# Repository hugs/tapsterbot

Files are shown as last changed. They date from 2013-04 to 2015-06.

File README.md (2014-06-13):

## Tapster - Mobile Automation Robot

<span>
    Tapsterbot
</span>

##Dependencies
- Node.js
- One Tapster robot

##Getting Started

1. Download and install the Arduino Client: [http://arduino.cc/en/Guide/HomePage](http://arduino.cc/en/Guide/HomePage)
2. Follow the setup procedure, and use the "blink" test script to verify your Arduino is working.
3. From the Arduino IDE upload the "Firmata" script: File -> Open -> Examples > Firmata > StandardFirmata
4. Install the dependencies: `cd software; npm install`
5. Start'er up: `node src/bot.js`
6. Start dancing: `dance()`
7. Stop dancing: `chill()`
8. Start moving: `go(0,0,-140)`

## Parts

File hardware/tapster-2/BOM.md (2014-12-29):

## Tapster Bill of Materials:

### Bitbeam
    3D Print:
    Qty     Description
    4       3x1 beam
    5       9x1 beam
    2       11x1 plate
    12      Coupler
    3       Servo mount
    1       Stylus holder
    3       Upper arm

    3D Print or Mill:
    Qty     Description
    1       Top plate
    1       Base plate
    3       Side plate
    1       Arduino plate

### Indigo.com
    Qty     Description                                             Part #          Unit Price
    24      Rod magnet, D5 x 7.5mm, Nd rare earth, N42              44201-7.5       $0.44

### McMaster-Carr
    Socket Bolts:
    Qty     Description     Long Description:                               Part #     Unit Price
    5       4-40 1/2 in     Black-Oxide Alloy Steel Socket Head Cap Screw   91251A110   $8.34 per pack of 100
    6       6-32 3/4 in     Black-Oxide Alloy Steel Socket Head Cap Screw   91251A151   $8.50 per pack of 100
    30      10-32 3/4 in    Black-Oxide Alloy Steel Socket Head Cap Screw   91251A345   $9.93 per pack of 100
    4       10-32 1 in      Black-Oxide Alloy Steel Socket Head Cap Screw   91251A347   $7.82 per pack of 50     

    Hex Nuts:
    Qty     Description             Long Description:                                       Part #      Unit Price
    5       4-40 nuts               Black Nylon 6/6 Hex Nut                                 94812A200   $5.63 per pack of 100
    6       6-32 nuts               Zinc-Plated Steel Machine Screw Hex Nut                 90480A007   $1.16 per pack of 100
    30      10-32 low-profile nuts  18-8 Stainless Steel Undersized Machine Screw Hex Nut   90730A411   $6.18 per pack of 100

    Misc:
    Qty     Description                                 Long Description:                   Part #      Unit Price
    12      3/8" Steel ball bearing                                                         96455K54    $5.87 per pack of 250
    6       12cm 6-32 Zinc-plated steel threaded rod    (Sold in 6ft sections)              98914A007   $3.67 for 6ft

### Servocity
    Qty     Description                                             Part #          Unit Price
    3       Hitec HS-311 servo (clockwise rotation)                 31311S00        $7.99

### Staples
    Qty     Description     Long Description                        Part #          Unit Price
    1       Tablet stylus   QVS ISE-SV Extending Mini-Stylus        IM1NZ0711       $3.99

## Electronics:

### Adafruit.com
    Qty     Description     Long Description                                    Part #          Unit Price
    1       Power adaptor   9 VDC 1000mA regulated switching power adapter      63              $6.95
    
### Amazon.com
    Qty     Description                                                         Part #          Unit Price
    1       SainSmart Sensor Shield Digital Analog Module V4                    B006TQ314G      $12.80

### Jameco.com
    Qty     Description             Long Description                            Part #          Unit Price
    1       Arduino Uno             MCU,ARDUINO UNO R3,DIP,14DI                 2151486         $29.95
    1       USB cable               CABLE,USB2.0,A/B,3',BLACK                   222608          $1.95
    1       Alligator clip          ALLIGATOR CLIP TEST LEADS, 24 AWG WIRE      2185483         $1.95

## Tools:

### McMaster-Carr
    Screwdrivers:
    Qty     Description         Long Description:                           Part #:     Unit Price:     Note:
    1       3/32 hex driver     Comfort Grip Ball Driver                    5497A25     $2.27           For 4-40 screws
    1       7/64 hex driver     Comfort Grip Ball Driver                    5497A26     $2.31           For 6-32 screws
    1       5/32 hex driver     Comfort Grip Ball Driver                    5497A29     $2.69           For 10-32 screws
    1       5/16 wrench         Miniature Inch Combination Wrench           5443A28     $10.69          For 10-32 nuts
    1       Philips #1 driver   Ultra-Grip Screwdriver with Antislip Tip    55095A32    $3.61           For servo mount

## Materials:
For 3D Printers:
ABS plastic from Ultimachine

For CNC Mills:
Plywood and Basswood from Blick Arts / Midwest Products

## Miscellaneous:

### Uline
    Qty     Description
    1       8X8x14 box
    1       Red bag

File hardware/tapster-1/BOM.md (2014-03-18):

## Tapster Bill of Materials:

### Bitbeam
    3D Print:
    Qty     Description
    12      2x1 beam
    8       3x1 beam
    6       5x1 beam
    5       9x1 beam
    2       11x1 plate
    6       17x1 plate
    3       Upper arm    
    3       Servo mount
    1       Stylus holder

    3D Print or Mill:
    Qty     Description
    3       5x29 side plate
    1       Arduino plate
    1       Base plate    
    1       Top plate

### McMaster-Carr
    Socket Bolts:
    Qty     Description     Long Description:                               Part #     Unit Price
    4       4-40 1/2 in     Black-Oxide Alloy Steel Socket Head Cap Screw   91251A110   $8.34 per pack of 100
    6       6-32 3/4 in     Black-Oxide Alloy Steel Socket Head Cap Screw   91251A151   $8.50 per pack of 100
    50      10-32 3/4 in    Black-Oxide Alloy Steel Socket Head Cap Screw   91251A345   $9.93 per pack of 100
    10      10-32 1 in      Black-Oxide Alloy Steel Socket Head Cap Screw   91251A347   $7.82 per pack of 50
    6       10-32 1 1/4 in  Black-Oxide Alloy Steel Socket Head Cap Screw   91251A349   $10.94 per pack of 50

    Hex Nuts:
    Qty     Description             Long Description:                                       Part #      Unit Price
    4       4-40 nuts               Black Nylon 6/6 Hex Nut                                 94900A005   $5.47 per pack of 100
    6       6-32 nuts               Zinc-Plated Steel Machine Screw Hex Nut                 90480A007   $1.16 per pack of 100
    48      10-32 low-profile nuts  18-8 Stainless Steel Undersized Machine Screw Hex Nut   90730A411   $6.18 per pack of 100
    18      10-32 lock nuts         Zinc-Plated Grade 2 Steel Nylon-Insert Hex Locknut      90631A411   $2.81 per pack of 100

### Jameco
    Qty     Description             Long Description                            Part #          Unit Price
    1       Arduino Uno             MCU,ARDUINO UNO R3,DIP,14DI                 2151486         $29.95
    1       Arduino proto-shield    SHIELD,PROTO,REV3,ASSEMBLED                 2152391         $15.95
    1       Breadboard              BREADBOARD,35x45x10mm,2.54mm HOLE SPACING   2109801         $4.95
    2       Jumper Wires            WIRE JUMPER REINFORCD,4"L,W/R               126342          $5.95
    1       USB cable               CABLE,USB2.0,A/B,3',BLACK                   222608          $1.95
    1       Alligator clip          ALLIGATOR CLIP TEST LEADS, 24 AWG WIRE      2185483         $1.95
    3       3-pin headers           HEADER,.1"ST MALE,1RW,3PIN                  109576          $0.35

### Servocity
    Qty     Description                                             Part #          Unit Price
    3       Hitec HS-311 servo (clockwise rotation)                 31311S00        $7.99

### Staples
    Qty     Description     Long Description                        Part #          Unit Price
    1       Tablet stylus   QVS ISE-SV Extending Mini-Stylus        IM1NZ0711       $3.99

## Tools:

### McMaster-Carr
    Screwdrivers:
    Qty     Description         Long Description:                           Part #:     Unit Price:     Note:
    1       3/32 hex driver     Comfort Grip Ball Driver                    5497A25     $2.27           For 4-40 screws
    1       7/64 hex driver     Comfort Grip Ball Driver                    5497A26     $2.31           For 6-32 screws
    1       5/32 hex driver     Comfort Grip Ball Driver                    5497A29     $2.69           For 10-32 screws
    1       3/8 nut driver      Comfort-Grip Inch NutdriversFor             53765A16    $3.58           For 10-32 lock nuts
    1       5/16 wrench         Miniature Inch Combination Wrench           5443A28     $10.69          For 10-32 nuts
    1       Philips #1 driver   Ultra-Grip Screwdriver with Antislip Tip    55095A32    $3.61           For servo mount

## Materials:
For 3D Printers:
ABS plastic from Ultimachine

For CNC Mills:
Plywood and Basswood from Blick Arts / Midwest Products

## Miscellaneous:

### Uline
    Qty     Description
    1       8X8x14 box
    1       Red bag

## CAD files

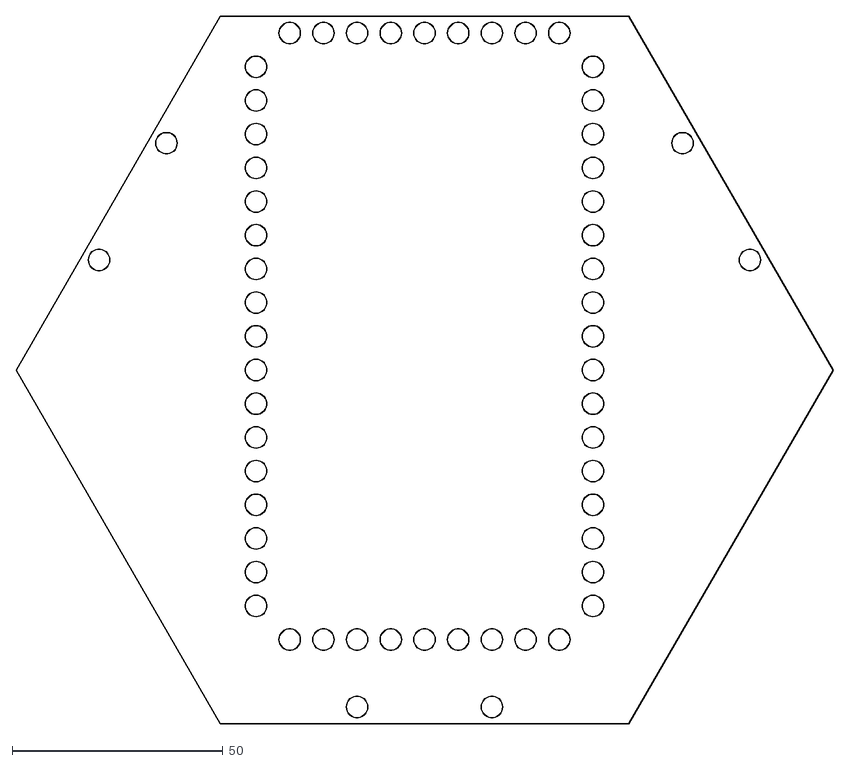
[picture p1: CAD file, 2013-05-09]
hardware/tapster-1/dxf/base.dxf
194.0 x 168.0

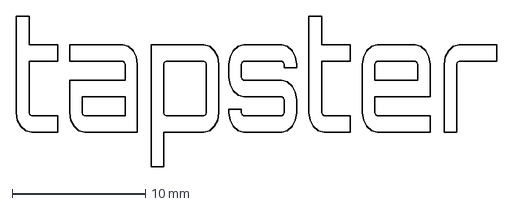
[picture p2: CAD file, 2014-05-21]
hardware/tapster-1/scad/tapster-smaller.dxf
36.1 x 11.3 mm

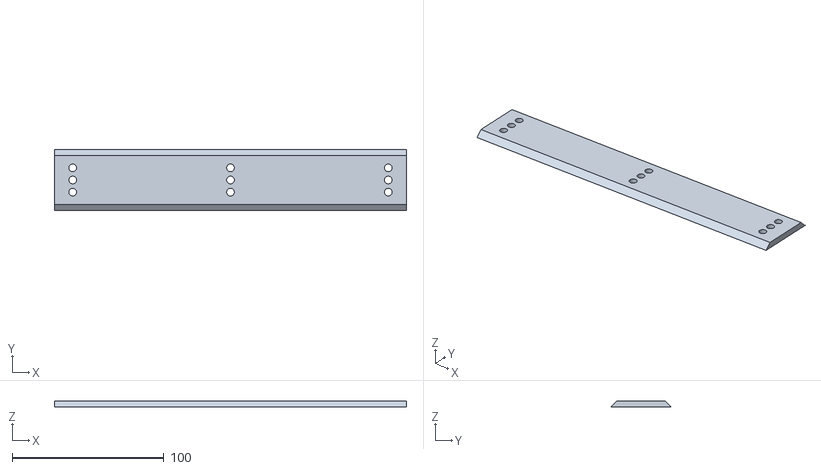
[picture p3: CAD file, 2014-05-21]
hardware/tapster-1/stl/rail.stl
232.0 x 40.0 x 4.00

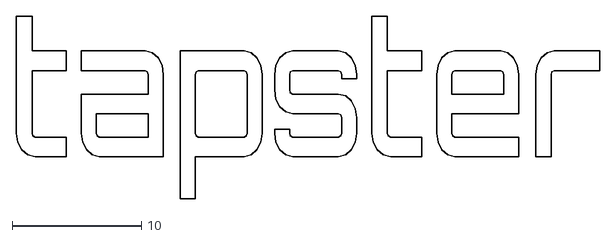
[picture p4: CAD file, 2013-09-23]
hardware/tapster-2-plus/scad/tapster.dxf
45.1 x 14.1

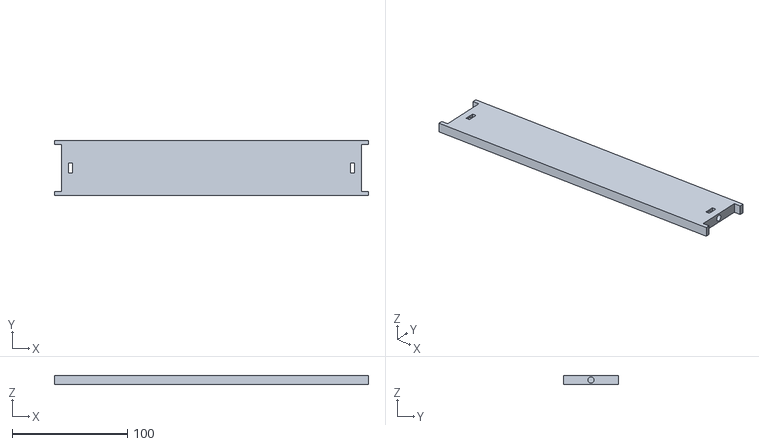
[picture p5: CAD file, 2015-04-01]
hardware/tapster-2-plus/stl/side.stl
272.0 x 47.8 x 8.00

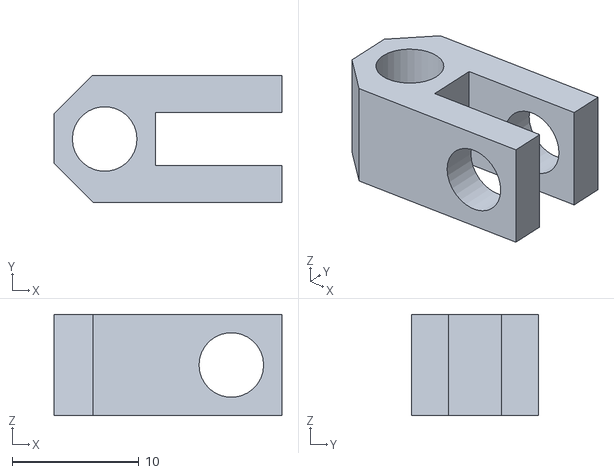
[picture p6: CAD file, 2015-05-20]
hardware/tapster-2-tablet/stl/joint.stl
18.0 x 10.0 x 8.00

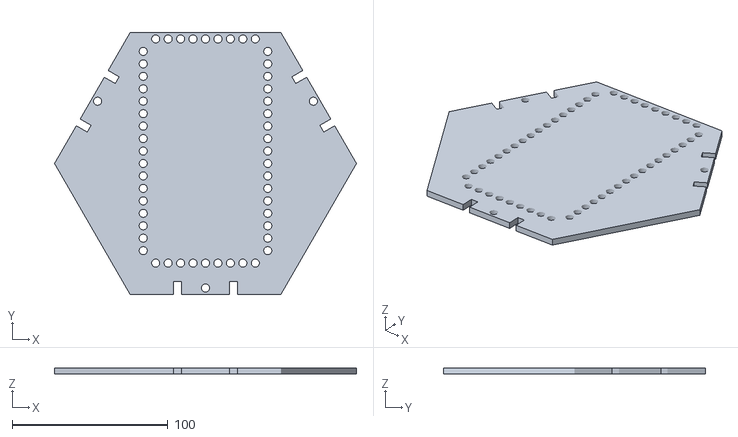
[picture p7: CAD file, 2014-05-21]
hardware/tapster-2/stl/base.stl
194.0 x 168.0 x 4.00

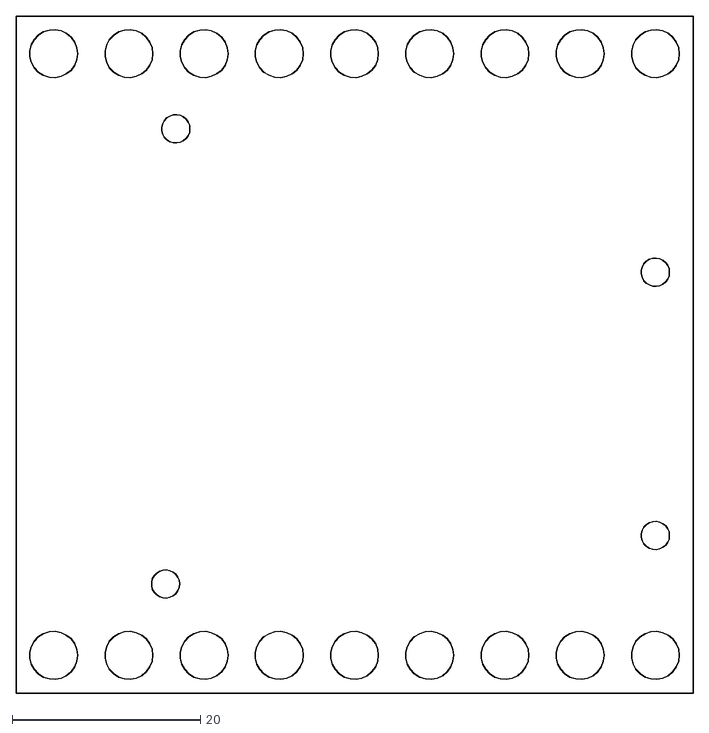
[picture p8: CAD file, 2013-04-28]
hardware/tapster-1/dxf/arduino-plate.dxf
72.0 x 72.0

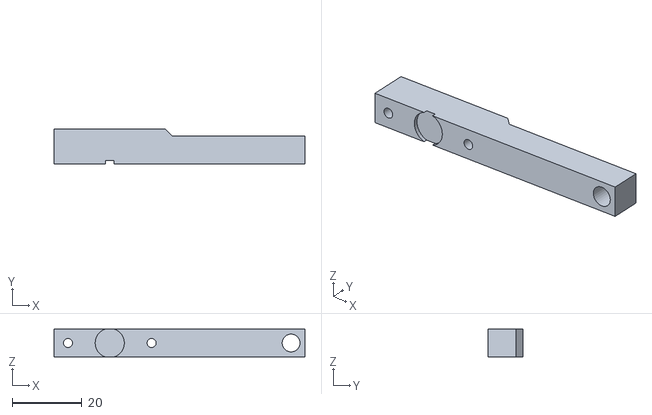
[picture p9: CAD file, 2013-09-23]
hardware/tapster-1/stl/upper-arm.stl
72.0 x 10.0 x 8.00

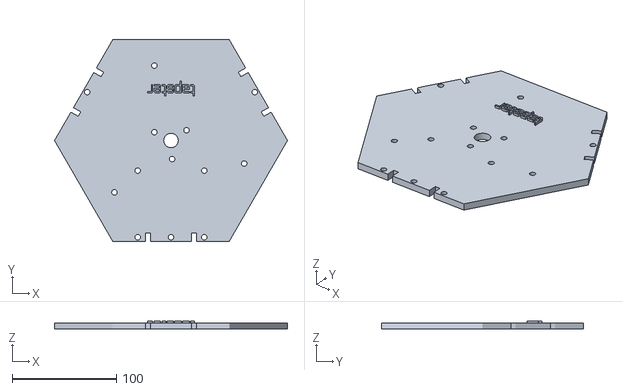
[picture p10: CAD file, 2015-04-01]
hardware/tapster-2-plus/stl/top.stl
224.0 x 194.0 x 8.00

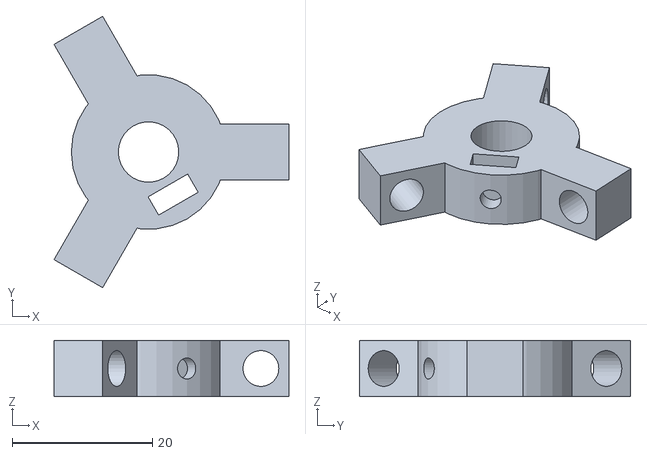
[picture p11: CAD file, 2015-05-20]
hardware/tapster-2-tablet/stl/stylus-holder.stl
33.5 x 38.6 x 8.00

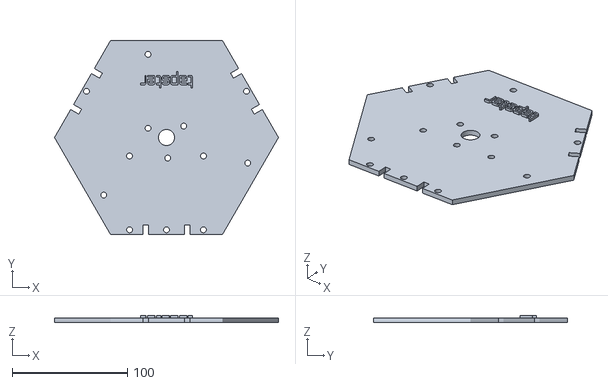
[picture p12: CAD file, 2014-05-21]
hardware/tapster-2/stl/top.stl
194.0 x 168.0 x 6.00

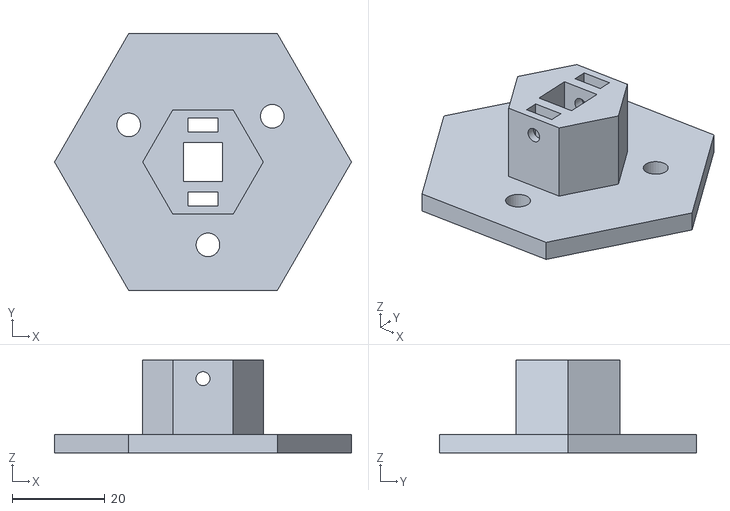
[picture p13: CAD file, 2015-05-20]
hardware/tapster-2-tablet/stl/camera-mount.stl
64.0 x 55.4 x 20.0

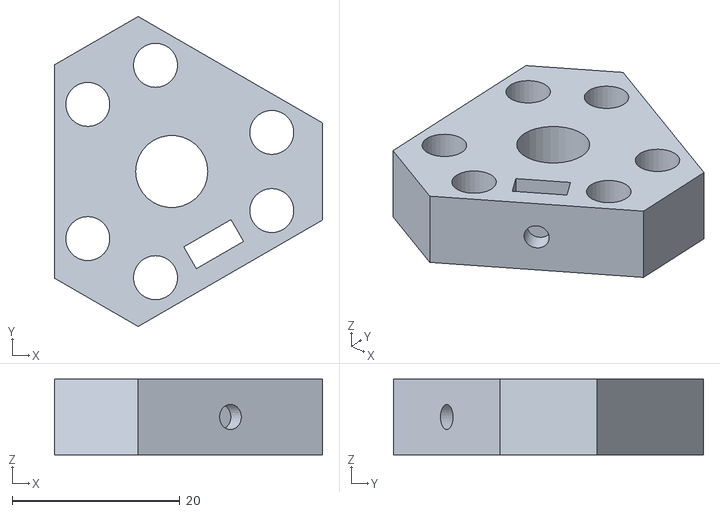
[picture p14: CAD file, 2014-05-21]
hardware/tapster-2/stl/stylus-holder.stl
32.0 x 37.0 x 9.00

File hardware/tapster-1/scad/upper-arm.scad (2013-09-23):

// Description: "Tapster - Mobile Automation Robot"
// Project home: http://tapsterbot.com

beam_width     = 8;
hole_diameter  = 5.1;
hole_radius    = hole_diameter / 2;
beam_length = 72;

difference() {
    // Draw the beam...
    union(){
        cube([beam_length,beam_width,beam_width]);

        translate([0,6,0])
        cube([32,4,8]);

        translate([32.0,4.35,0])
        rotate([0,0,45])
        cube([4,4,8]);
    }
    
    rotate([90,0,0])
    translate([16,4,-1])
    cylinder(r=4.2, h=5, $fn=30);

    // Hole #1 for servo
    rotate([90,0,0])
    translate([4,beam_width/2,-12])
    cylinder(r=1.3, h=14, $fn=30);

    // Hole #2 for servo
    rotate([90,0,0])
    translate([28,beam_width/2,-12])
    cylinder(r=1.3, h=14, $fn=30);

    // Hole for connecting to lower arm
    rotate([90,0,0])
    translate([4+8*8,beam_width/2,-10])
    cylinder(r=hole_radius, h=12, $fn=30);
}

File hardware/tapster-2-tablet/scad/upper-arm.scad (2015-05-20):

// Description: Upper arm for Tapster 2 Plus
// Project home: http://tapsterbot.com

// Slicer settings
// Infill density: 0.5
// Fill pattern: line
// Top/bottom fill pattern: rectilinear

beam_width     = 8;
hole_diameter  = 5.25;
hole_radius    = hole_diameter / 2;
beam_length = beam_width * 20.5;



difference() {
    // Draw the beam...
    union(){
        cube([beam_length-16,beam_width,beam_width*2]);

        translate([0,0,0])
        cube([beam_length,beam_width,beam_width+4]);

        translate([0,6,0])
        cube([32,4,16]);

        translate([32.0,4.35,0])
        rotate([0,0,45])
        cube([4,4,16]);

        //rotate(90)
        //translate([-8,-beam_length,0])
        //cube([24,8,8]);
    }

    translate([-2,5,32])
    rotate([0,45,0])
    cube([32,32,32], center=true);

    translate([-2,5,-16])
    rotate([0,45,0])
    cube([32,32,32], center=true);

    // Servo mount - center
    rotate([90,0,0])
    translate([16,8,-1])
    cylinder(r=4.2, h=5, $fn=30);

    // Hole #1 for servo
    rotate([90,0,0])
    translate([4,8,-12])
    cylinder(r=1.3, h=14, $fn=30);

    // Hole #2 for servo
    rotate([90,0,0])
    translate([28,8,-12])
    cylinder(r=1.3, h=14, $fn=30);

    rotate([90,0,0])
    translate([beam_length-4,8,-14])
    cylinder(r=hole_radius, h=20, $fn=30);

}

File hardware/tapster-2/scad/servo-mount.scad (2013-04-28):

// From: http://www.servocity.com/html/hs-311_standard.html
A = 19.82;
B = 13.47;
C = 33.79;
D = 10.17;
E = 9.66;
F = 30.22;
G = 11.68;
H = 26.67;
J = 52.84;
K = 9.35;
L = 4.38;
M = 39.88;
X = 3.05;

// Clearance hole for either 6-32 or M3 bolt
servo_hole_radius = 3.8/2;

// Bitbeam (and Lego Technic) beam width
beam_width = 8;

// Bitbeam (and Lego Technic) hole size
hole_diameter = 5.2;
hole_radius   = hole_diameter / 2;

module servo() {
    x1 = (J-(B+C))/2;
    y1 = (A-D)/2;

    x2 = x1+B+C;
    y2 = y1;

    // 2 mounting holes
    translate([x1,y1,-2])
    cylinder(r=servo_hole_radius, h=12, $fn=30);

    translate([x2,y2,-2])
    cylinder(r=servo_hole_radius, h=12, $fn=30);

    // servo hole
    x_servo = (J-40.5)/2;
    y_servo = 0;
    translate([x_servo, y_servo,-2])
    cube([40.5,20,12]);
}


module box() {
    difference() {
        cube([7*beam_width,2.5*beam_width-1,8]); 

        for (x=[beam_width/2 : beam_width : 7*beam_width]) {
            translate([x,beam_width/2,-2])
            cylinder(r=hole_radius, h=12, $fn=30);
        }
    }
}


difference() {
    box();
    
    translate([(7*beam_width-J)/2,(5*beam_width-A)/2])
    servo();
}

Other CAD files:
hardware/tapster-1/stl/top.stl
hardware/tapster-1/stl/side.stl
hardware/tapster-2-tablet/stl/camera-holder.stl
hardware/tapster-2/stl/coupler.stl
hardware/tapster-2/scad/upper-arm.scad
hardware/tapster-1/dxf/side.dxf
hardware/tapster-1/dxf/top.dxf
hardware/tapster-1/scad/5x5-plate.scad
hardware/tapster-1/scad/6x5-plate.scad
hardware/tapster-1/scad/base.scad
hardware/tapster-1/scad/bitbeam-beam.scad
hardware/tapster-1/scad/bitbeam-plate.scad
hardware/tapster-1/scad/rail.scad
hardware/tapster-1/scad/side.scad
hardware/tapster-1/scad/stylus-holder.scad
hardware/tapster-1/scad/top.scad
hardware/tapster-1/stl/beam-2x1.stl
hardware/tapster-1/stl/beam-3x1.stl
hardware/tapster-1/stl/beam-5x1.stl
hardware/tapster-1/stl/beam-9x1.stl
hardware/tapster-1/stl/plate-17x1.stl
hardware/tapster-1/stl/stylus-holder.stl
hardware/tapster-2-plus/scad/base.scad
hardware/tapster-2-plus/scad/side.scad
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

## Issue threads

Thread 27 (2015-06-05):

OSX Yosemite: node src/bot.js run Errors

Chasen88, 2015-06-05:
So following the README, I was able to flash the arduino and run 'npm install' with success. However, when running 'node src/bot.js I recieve the following error. I am not really sure where to start with debugging.

mtchasen:software chasen$ node src/bot.js
/Users/chasen/workspace/tapsterbot/software/node_modules/johnny-five/node_modules/firmata/lib/firmata.js:1239
  this.transport.write(new Buffer([START_SYSEX, SAMPLING_INTERVAL, (safeint &
                 ^
TypeError: undefined is not a function
    at Board.setSamplingInterval (/Users/chasen/workspace/tapsterbot/software/node_modules/johnny-five/node_modules/firmata/lib/firmata.js:1239:18)
    at null.<anonymous> (/Users/chasen/workspace/tapsterbot/software/node_modules/johnny-five/node_modules/firmata/lib/firmata.js:545:14)
    at g (events.js:199:16)
    at emit (events.js:104:17)
    at Object.SYSEX_RESPONSE.(anonymous function) (/Users/chasen/workspace/tapsterbot/software/node_modules/johnny-five/node_modules/firmata/lib/firmata.js:176:9)
    at null.<anonymous> (/Users/chasen/workspace/tapsterbot/software/node_modules/johnny-five/node_modules/firmata/lib/firmata.js:481:48)
    at SerialPort.emit (events.js:107:17)
    at Object.module.exports.raw [as parser] (/Users/chasen/workspace/tapsterbot/software/node_modules/johnny-five/node_modules/serialport/parsers.js:8:13)
    at Object.SerialPort.opts.dataCallback (/Users/chasen/workspace/tapsterbot/software/node_modules/johnny-five/node_modules/serialport/serialport.js:181:12)
    at SerialPortFactory.SerialPort._emitData (/Users/chasen/workspace/tapsterbot/software/node_modules/johnny-five/node_modules/serialport/serialport.js:396:20)

rwaldron, 2015-06-05:
What version of Node are you using?

Chasen88, 2015-06-05:
Hello Rick,

It looks like I am running V0.12.4

 node -v
v0.12.4

On Fri, Jun 5, 2015 at 11:45 AM Rick Waldron <notifications@github.com>
wrote:

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

rwaldron, 2015-06-05:
@Chasen88 Use `nvm` or similar to hop back to a version of node in the 0.10.x series then do `npm rebuild` in the `software/` dir and try re-running

rwaldron, 2015-06-05:
Did `npm install` fail or produce an npm debug log?

Chasen88, 2015-06-05:
@rwaldron Ill give rolling the version back a shot. The install appeared to be successfully, I don't seen any log files within the directory.

Chasen88, 2015-06-05:
@rwaldron So it turns out that if I pull the repo for johnny-five directly and install it from git, the error goes away and I am able to run the code. So I dont know what was wrong originally, but it works now.

rwaldron, 2015-06-05:
I think there is still an issue, because it should install from npm without issues.

rwaldron, 2015-06-05:
I think I figured it out, Tapster bot has a very old version of Johnny-Five.

Chasen88, 2015-06-05:
@rwaldron Sorry for prematurely closing the issue. Glad you were able to figure it out.

hugs, 2015-06-10:
@rwaldron @Chasen88 Thanks for the fixes. And sorry for the headaches! It had been too long since I had downloaded and installed everything from scratch with all the latest versions. I can also confirm that this fix makes it so Tapster works with the latest io.js, too. (io.js version 2.2.1 as I write this...)

Closed 2015-06-05.

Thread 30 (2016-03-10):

node bot.js unspecified "error" event

hc89yk, 2016-03-10:
So following the README, I was able to flash the arduino and run 'npm install' with success. However, when running 'node src/bot.js I recieve the following error:

Error: Uncaught, unspecified "error" event. ([object Object])
    at Board.emit (events.js:144:17)
    at Board.log (C:\Users\HCC\Desktop\tapsterbot-master\software\node_modules\j
ohnny-five\lib\board.js:630:8)
    at Board.(anonymous function) [as error] (C:\Users\HCC\Desktop\tapsterbot-ma
ster\software\node_modules\johnny-five\lib\board.js:641:14)
    at Board.<anonymous> (C:\Users\HCC\Desktop\tapsterbot-master\software\node_m
odules\johnny-five\lib\board.js:418:14)
    at Timer.listOnTimeout (timers.js:92:15)

I tried evrything what I found on the internet but nothing changed.

What can I do now?

rwaldron, 2016-03-10:
I think you might be missing most of the error message here, it should've displayed this:

```
$ node eg/keypad-MPR121_SHIELD.js
1457645312961 Device(s) /dev/cu.usbmodem1421
1457645312971 Connected /dev/cu.usbmodem1421
1457645322977 Device or Firmware Error A timeout occurred while connecting to the Board.

Please check that you've properly flashed the board with the correct firmware.
See: https://github.com/rwaldron/johnny-five/wiki/Getting-Started#trouble-shooting

If connecting to a Leonardo or Leonardo clone, press the 'Reset' button on the board, wait approximately 11 seconds for complete reset, then run your program again.
events.js:146
      throw err;
      ^

Error: Uncaught, unspecified "error" event. ([object Object])
    at Board.emit (events.js:144:17)
    at Board.log (/Users/rwaldron/clonez/johnny-five/lib/board.js:630:8)
    at Board.(anonymous function) [as error] (/Users/rwaldron/clonez/johnny-five/lib/board.js:641:14)
    at Board.<anonymous> (/Users/rwaldron/clonez/johnny-five/lib/board.js:418:14)
    at Timer.listOnTimeout (timers.js:92:15)
```

This is caused by one of several possible things:

- StandardFirmataPlus isn't actually flashed to the board
- The board is browning out due to some power over-draw
- The board is shorting
- The cable is faulty

hc89yk, 2016-03-11:
Hi,

I only get that error message, that is all what cmd show.

Why I need to use StandardFirmataPlus?
My readme file say this:

1. Download and install the Arduino Client: [http://arduino.cc/en/Guide/HomePage](http://arduino.cc/en/Guide/HomePage)
2. Follow the setup procedure, and use the "blink" test script to verify your Arduino is working.
3. From the Arduino IDE upload the "Firmata" script: File -> Open -> Examples > Firmata > StandardFirmata
4. Install the dependencies: `cd software; npm install`
5. Start'er up: `node src/bot.js`
6. Start dancing: `dance()`
7. Stop dancing: `chill()`
8. Start moving: `go(0,0,-140)`

Can I use FirmataPlus?

rwaldron, 2016-03-11:
Awesome! Glad you resolved the issue :)

Closed 2016-03-11.

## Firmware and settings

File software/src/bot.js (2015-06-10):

five = require("johnny-five");
ik = require("./ik");
board = new five.Board({
  debug: false
});

board.on("ready", function() {
    // Setup
    servo1 = five.Servo({
        pin: 9,
        range: [0,90]
    });
    servo2 = five.Servo({
        pin: 10,
        range: [0,90]
    });
    servo3 = five.Servo({
        pin: 11,
        range: [0, 90]
    });

    board.repl.inject({
      servo1: servo1,
      s1: servo1,
      servo2: servo2,
      s2: servo2,
      servo3: servo3,
      s3: servo3,
    });

    // Move to starting point
    var max = 15;
    var min = 5;
    var range = max - min;
    servo1.to(min);
    servo2.to(min);
    servo3.to(min);

    var dance = function() {
      servo1.to(parseInt((Math.random() * range) + min, 10));
      servo2.to(parseInt((Math.random() * range) + min, 10));
      servo3.to(parseInt((Math.random() * range) + min, 10));
    };

    var dancer;

    start_dance = function() {
      if (!dancer) dancer = setInterval(dance, 250);
    }

    stop_dance = function() {
      if (dancer) {
        clearInterval(dancer);
        dancer = null;
      }
    }

    board.repl.inject({
      dance: start_dance,
      chill: stop_dance
    });


});


Number.prototype.map = function ( in_min , in_max , out_min , out_max ) {
  return ( this - in_min ) * ( out_max - out_min ) / ( in_max - in_min ) + out_min;
}

rotate = function(x,y) {
    var theta = -60;
    x1 = x * cos(theta) - y * sin(theta);
    y1 = y * cos(theta) + x * sin(theta);
    return [x1,y1]
}

reflect = function(x,y) {
    var theta = 0;
    x1 = x;
    y1 = x * sin(2*theta) - y * cos(2*theta);
    return [x1,y1]
}


// A sine function for working with degrees, not radians
sin = function(degree) {
    return Math.sin(Math.PI * (degree/180));
}

// A cosine function for working with degrees, not radians
cos = function(degree) {
    return Math.cos(Math.PI * (degree/180));
}


// TODO: pull out map values to config file or some other solution.
go = function(x, y, z) {
  reflected = reflect(x,y);
  rotated = rotate(reflected[0],reflected[1]);

  angles = ik.inverse(rotated[0], rotated[1], z);
  servo1.to((angles[1]).map( 0 , 90 , 8 , 90 ));
  servo2.to((angles[2]).map( 0 , 90 , 8 , 90 ));
  servo3.to((angles[3]).map( 0 , 90 , 8 , 90 ));
  console.log(angles);
}

position = function() {
  return ik.forward(servo1.last.degrees, servo2.last.degrees, servo3.last.degrees);
}

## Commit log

2013-04-28 Open source all the things!
    [arduino-plate.dxf, arduino-plate.scad, arduino-plate.stl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]
2013-04-29 First pass at a proper bill of materials.
2013-04-30 Control the bot with your browser
    Clean up / refactoring needed, but this should be the
    minimum necessary to drive the device remotely via your
    browser and the bot
2013-04-30 Fixed formatting.
    [bitbeam-beam.scad]
2013-05-09 Removing a few superfluous holes. I love that word. Superfluous.
    [base.dxf, base.scad, base.stl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]
2013-05-14 Adding center hole for easier servo wire routing. Good idea, @kastner!
    [top.dxf, top.scad, top.stl]
2013-06-30 Adding specifics about servo rotation
2013-07-25 Adding some text to the top plate.
    [top.scad, top.stl]
2013-08-02 Simplify Servo initializers
2013-09-23 Adding size option for Open Structures-compatibility
    [bitbeam-beam.scad]
2013-09-23 Fixed the kerning of the text on the top plate.
    [tapster.dxf, top.scad, top.stl]
2013-09-23 New and improved upper arm.
    [upper-arm.scad, upper-arm.stl]
2014-05-01 Fixing part size and calibration info
    [bot.js]
2014-05-01 X and Y axis are orientated properly.. finally
2014-05-07 Fixed Angry Birds demo.
    [bot.js]
2014-05-21 Massive dir cleanup. Adding Tapster 2 files.
    [5x5-plate.scad, 5x5-plate.stl, 6x5-plate.scad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]
2014-06-11 Update BOM with magnet part number and price.
2014-06-11 Added power adaptor part number and price
2014-06-11 Part number and price for Arduino sensor shield.
2014-06-13 Tapster 2 stl file cleanup. Closes issue #25
    [5x5-plate.stl, 6x5-plate.stl, beam-3x1.stl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]
2014-06-13 Now all the Tapster 2 parts are in the Tapster 2 directory.
    [arduino-plate.scad, arduino-plate.stl, arduino.scad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]
2014-12-29 The beginning of support for iPhone 6 plus...
    [base.scad]
2015-04-01 Parts for Tapster 2 Plus
    [base.scad, base.stl, coupler.scad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]
2015-04-28 Start of Tapster 2T (for Tablets)
    [base.scad, base.stl]
2015-05-20 Design files for Tapster 2T
    [base.scad, bracket.scad, bracket.stl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]
2015-06-05 Servo doesn't emit errors
    [bot.js]
